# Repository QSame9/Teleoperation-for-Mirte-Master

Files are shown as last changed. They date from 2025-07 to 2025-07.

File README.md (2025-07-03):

# Teleoperation-for-Mirte-Master

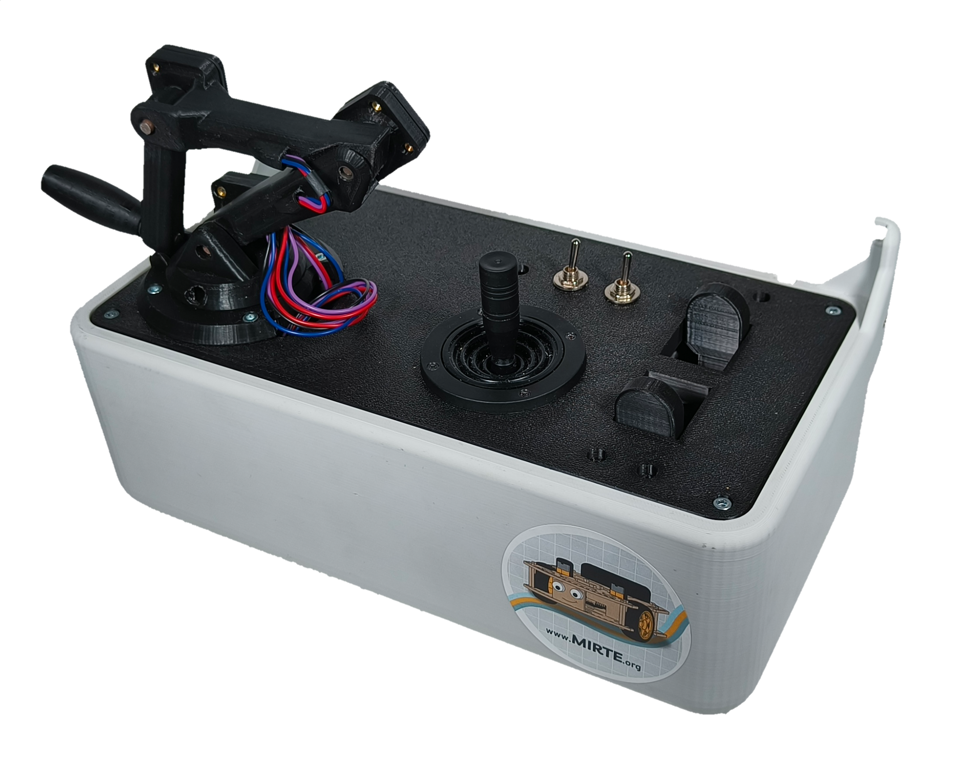
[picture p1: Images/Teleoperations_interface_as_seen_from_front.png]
<figure class="image"><figcaption>Teleoperation interface as seen from front, image by Duncan Bijkerk and Quita Carriere</figcaption></figure>

Authors: Ynze Visser, Quita Carriere, Aditya Swami, Duncan Bijkerk  
Repository: [GitHub page](https://github.com/QSame9/Teleoperation-for-Mirte-Master)  

A physical remote controller interface for the Mirte Master. This project is part of the Bachelor End Project for Mechanical Engineering students at the TU Delft. It was commissioned by the Cognitive Robotics department of the TU Delft.  

# Use of the Teleoperation interface
The Teleoperation interface, here on out also called remote controller, is made for the Mirte Master,  
 often called Mirte, for more info see the [Mirte site](https://mirte.org/) and the [Mirte GitHub](https://github.com/mirte-robot).

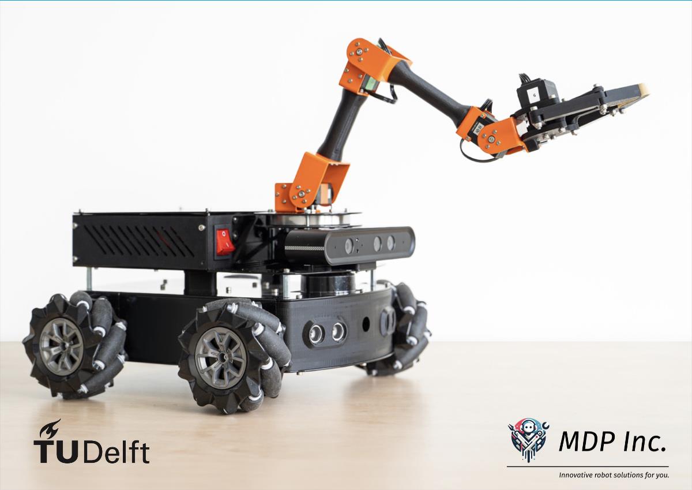
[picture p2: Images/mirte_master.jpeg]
<figure class="image"><figcaption>Mirte Master, image by Chris Pek</figcaption></figure>

The arm movement of the Mirte is controlled by the arm of the controller, mimicking the angular position of each joint. All joints can therefor be controlled in 0th order. To reach the full workspace of the Mirte, a 1st order movement is coded into the periferal working space of the yaw joint of the controller. The Mirte yaw joint can only move 180&deg;, so to reach the back side of the Mirte one of the swithes is made to mirror the movement of all of the arm joints except for the yaw.

The gripper of the Mirte is controlled by the pincher mechanism of the controller, see image below.

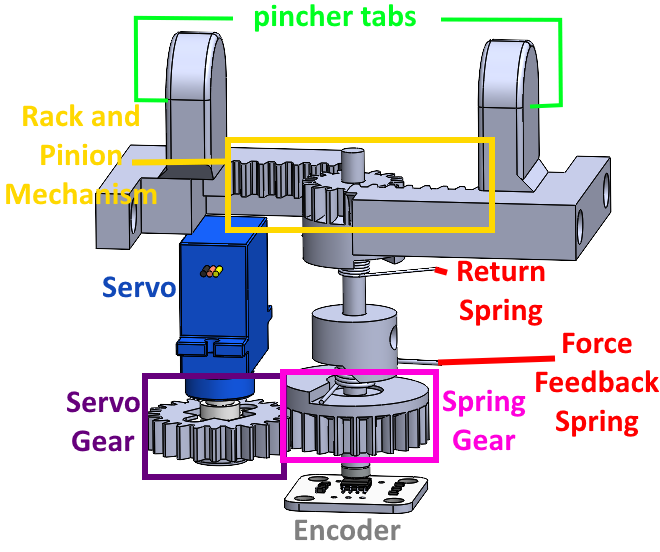
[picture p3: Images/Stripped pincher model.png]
<figure class="image"><figcaption>Pincher CAD close up</figcaption></figure>

Here the linear pinching is transfered via a rack and pinion mechanism to be read out by an angular encoder. This is mapped to the workspace of the gripper. The information is also sent to a force simulator, as to get the force that the force feedback needs to apply. This force feedback is done through Series Elestic Actuation. The servo motor is turned to make the tortion spring compress the correct amount to apply a stiffness to the pincher tabs that the operator holds. The other spring in the mechanism is a return spring, so the tabs open again once the operator lets go.

The driving is done through a simple, off-the-shelf joystick. The Mirte can drive in both holonomic and angular drive methods, and a switch allows for changing the driving style. Due to sensor bias in the joystick, a calibration is done during startup, so the neutral position is determined.

[Here](https://youtube.com/shorts/fPgHeI3LzEk) is a video of the teleoperation interface in action. Some of the delay issues have been resoved since the making of this video.

All the files of the software, CAD models, and electronics can be found in this GitHub repository. The written report for the Bachelor End Project, as well as the presentations given for the course and the files used for analysis can be found in this repository as well.

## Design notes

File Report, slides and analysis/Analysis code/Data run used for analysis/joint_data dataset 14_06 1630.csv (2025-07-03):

t_yaw_enc | data_yaw_enc | t_yaw_mirte | data_yaw_mirte | t_shoulder_enc | data_shoulder_enc | t_shoulder_mirte | data_shoulder_mirte | t_elbow_enc | data_elbow_enc | t_elbow_mirte | data_elbow_mirte | t_wrist_enc | data_wrist_enc | t_wrist_mirte | data_wrist_mirte | t_gripper_enc | data_gripper_enc | t_gripper_mirte | data_gripper_mirte
1.556199312 | -0.03132767 | 2.202921152 | -0.00418879 | 1.589461088 | 1.361505651 | 2.232694387 | 0.963072658 | 1.618501425 | -2.737175102 | 2.273548841 | -1.589994907 | 1.64706707 | -1.562238216 | 2.288056612 | -1.433962464 | 1.676944733 | 0.00644949 | 2.300480366 | 0.446106166
1.570454597 | -0.03132767 | 2.35274744 | 0 | 1.603838921 | 1.361505651 | 3.715931416 | 0.971450269 | 1.639005899 | -2.737175102 | 2.297421455 | -1.594183683 | 1.672877789 | -1.562238216 | 2.353654146 | -1.429773688 | 1.70294404 | 0.00644949 | 2.315000296 | 0.44191736
1.603398561 | -0.03132767 | 2.376379251 | -0.00418879 | 1.640059948 | 1.361505651 | 3.736181498 | 1.000771761 | 1.671754122 | -2.737175102 | 2.315362453 | -1.589994907 | 1.704828024 | -1.562238216 | 2.376704216 | -1.433962464 | 1.735801458 | 0.00644949 | 2.33398509 | 0.433539778
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

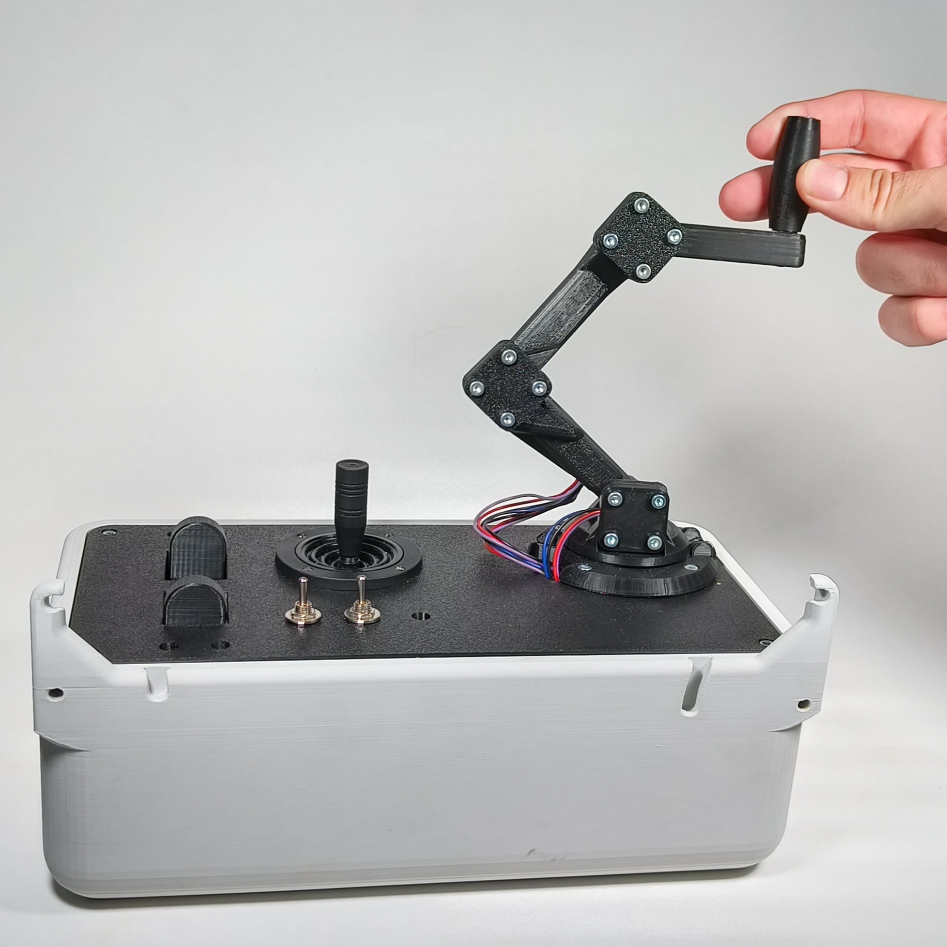
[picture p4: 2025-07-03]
Images/Teleoperations_interface_as_seen_from_operator.jpg

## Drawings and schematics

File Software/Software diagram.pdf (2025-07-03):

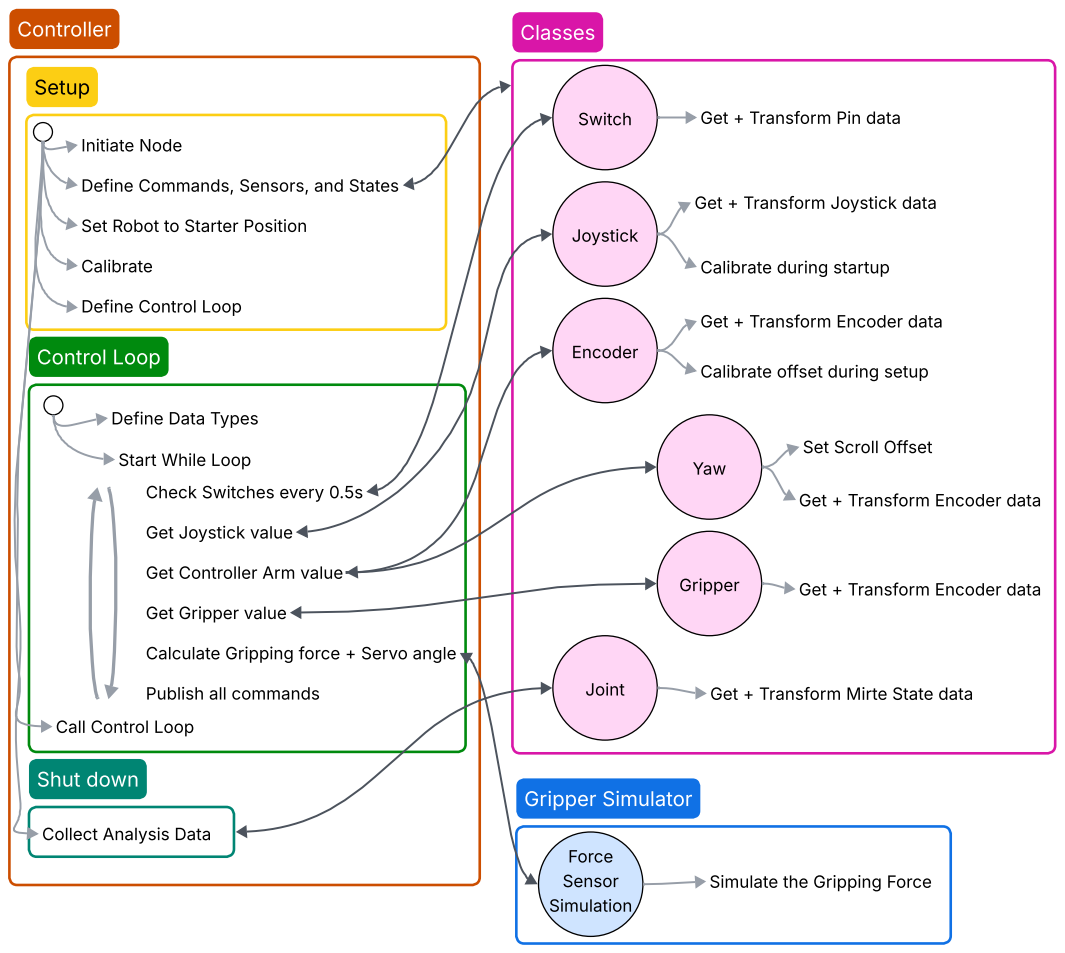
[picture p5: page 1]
Classes; Gripper Simulator; Controller; Setup; Shut down; Encoder; Gripper; Joint; Switch; Joystick; Yaw; Initiate Node; Calibrate; Control Loop; Force Sensor Simulation; Simulate the Gripping; Force

Get + Transform Pin data

Define Commands, Sensors, and States

Get + Transform Joystick data

Set Robot to Starter Position

Calibrate during startup

Define Control Loop

Get + Transform Encoder data

Calibrate offset during setup

Define Data Types

Set Scroll Offset

Start While Loop
Check Switches every 0.5s

Get Joystick value

Get Controller Arm value

Get Gripper value

Calculate Gripping force + Servo angle

Publish all commands

Get + Transform Mirte State data

Call Control Loop

Collect Analysis Data

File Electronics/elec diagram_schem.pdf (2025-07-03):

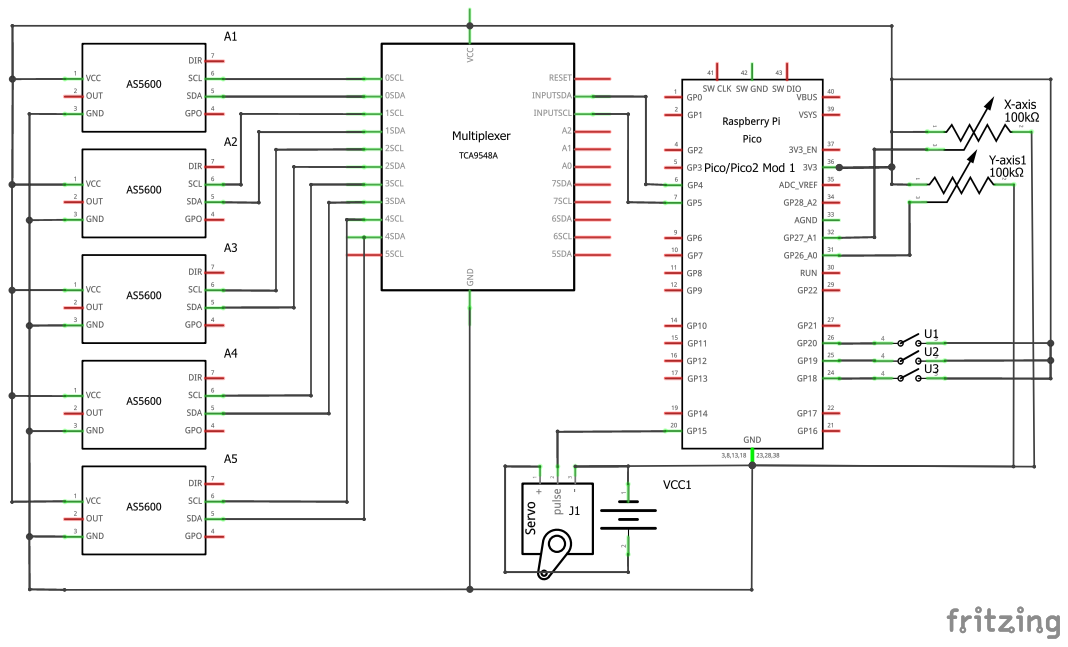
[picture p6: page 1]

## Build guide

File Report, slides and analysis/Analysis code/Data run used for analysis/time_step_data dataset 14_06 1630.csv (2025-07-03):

get switch value | get base input | get arm input | get gripper input | publish base | publish arm | publish gripper | publish servo
0.002441883 | 1.24E-05 | 3.15E-05 | 6.37E-05 | 0.000226259 | 0.000181913 | 0.023518324 | 4.77E-06
2.86E-06 | 1.26E-05 | 2.79E-05 | 5.17E-05 | 0.000206232 | 0.000162125 | 0.010455847 | 5.25E-06
4.05E-06 | 1.67E-05 | 3.39E-05 | 6.32E-05 | 0.000235558 | 0.000165462 | 0.01342535 | 5.25E-06
3.10E-06 | 1.24E-05 | 2.65E-05 | 5.17E-05 | 0.000187397 | 0.000145912 | 0.010587692 | 5.48E-06
3.81E-06 | 1.29E-05 | 3.00E-05 | 4.77E-05 | 0.000200272 | 0.000172138 | 0.015842915 | 4.53E-06
3.10E-06 | 1.19E-05 | 2.62E-05 | 5.05E-05 | 0.000178099 | 0.000131845 | 0.014976025 | 4.29E-06
2.62E-06 | 1.22E-05 | 2.48E-05 | 5.01E-05 | 0.000179291 | 0.000127077 | 0.014565945 | 5.72E-06
3.81E-06 | 1.14E-05 | 2.62E-05 | 5.01E-05 | 0.000178576 | 0.000124454 | 0.011327982 | 5.72E-06
3.81E-06 | 1.05E-05 | 2.53E-05 | 4.60E-05 | 0.000180244 | 0.000198126 | 0.017859936 | 4.77E-06
2.62E-06 | 1.22E-05 | 2.57E-05 | 5.17E-05 | 0.000178099 | 0.000128984 | 0.015555382 | 4.53E-06
3.58E-06 | 1.24E-05 | 2.91E-05 | 4.94E-05 | 0.000240326 | 0.000151873 | 0.013943195 | 3.34E-06
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

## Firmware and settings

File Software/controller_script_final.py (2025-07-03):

"""
Project Name: Teleoperation interface of Mirte Master
File: controller_script_final.py
Description: Does the reading out and the publishing of commands for the Mirte Master

Author: Ynze Visser, Quita Carriere, Aditya Swami, Duncan Bijkerk
License: MIT
Repository: https://github.com/QSame9/Teleoperation-for-Mirte-Master

This file is part of the Bachelor End Project for Mechanical Engineering students at the TU Delft. 
It was commissioned by the Cognitive Robotics department of the TU Delft.


This file is distributed under the terms
of the MIT License. See the LICENSE file in the root of this repository
or visit https://opensource.org/licenses/MIT for more details.
"""
# ---- Import ----
import rospy
import numpy as np
from sensor_classes_final import Encoder, Joystick, Switch, YawEncoder, GripperEncoder, Joint
from gripper_simulator_file_final import GripperSimulator
import math
import csv
import pandas as pd
import time
# import data_collection_script

# load the specific message format required for joint commands
from std_msgs.msg import Float64MultiArray, Float32
from geometry_msgs.msg import Twist
from mirte_msgs.srv import SetServoAngle, GetPinValue, SetPinValue
from mirte_msgs.msg import ServoPosition, Intensity
from sensor_msgs.msg import JointState


# ---- Initialize controller node --------

# start a new ROS node
rospy.init_node('simple_controller_publisher')
# provide on-screen information
rospy.loginfo('The base_controller_publisher has started!')



# ---- Set the publishers and services to control the position of the Mirte Master --------

# create the publisher, tell it which topic to publish on
base_command_publisher = rospy.Publisher('/mobile_base_controller/cmd_vel', Twist, queue_size=10) 
# create the publisher, tell it which topic to publish on
arm_command_publisher = rospy.Publisher('/arm/joint_position_controller/command', Float64MultiArray, queue_size=10)
#create the service, serviceproxy is aan de client side, dus voor het verzenden
set_gripper_angle_service = rospy.ServiceProxy('/mirte/set_servoGripper_servo_angle', SetServoAngle, persistent = True)
set_pincher_servo_angle = rospy.ServiceProxy('/mirte_remote/mirte/set_gripper_cntlr_servo_angle', SetServoAngle, persistent = True)

# ---- General values --------

update_speed = 0.1
stiffness_gripper_spring = 2.08
yaw_offset = 0.51 #yaw on magnet
shoulder_offset = 2.1 #straight up
elbow_offset = 3.13 - 0.5 #straight up
wrist_offset = 4.50 #fully bent inwards
gripper_offset = 2.20 #fully open
servo_offset = math.radians(130) #graden
spring_engagement_angle = 0.60

def callback_states(msg):
    global joint_states_data
    joint_states_data = msg.position

# ---- define sensors on controller --------

yaw_encoder = YawEncoder('/mirte_remote/mirte/encoder/encoders/a', spring_engagement_angle, 
                        calibrating_angle = 0, scaling_factor = 1, first_order_control_gain = 2, offset = yaw_offset)
schoulder_encoder = Encoder('/mirte_remote/mirte/encoder/encoders/b', 
                        calibrating_angle = 0, offset = shoulder_offset)
elbow_encoder = Encoder('/mirte_remote/mirte/encoder/encoders/c', scaling_factor = -1,
                        calibrating_angle = 0, offset = elbow_offset)
wrist_encoder = Encoder('/mirte_remote/mirte/encoder/encoders/d', scaling_factor = -1,
                        calibrating_angle = 1.28, offset = wrist_offset) 
gripper_encoder = GripperEncoder('/mirte_remote/mirte/encoder/encoders/e', 
                        calibrating_angle = 0, offset = gripper_offset, scaling_factor = 1) #checken
joystick = Joystick('/mirte_remote/mirte/intensity/x_axis', 
                        '/mirte_remote/mirte/intensity/y_axis', 0.5 * 1/2040)
gripper_simulator = GripperSimulator()
#joint_states = rospy.Subscriber('/arm/joint_states', JointState, callback_states)

mirte_yaw_joint_state = Joint('/mirte/servos/servoRot/position')
mirte_schoulder_joint_state = Joint('/mirte/servos/servoShoulder/position')
mirte_elbow_joint_state = Joint('/mirte/servos/servoElbow/position')
mirte_wrist_joint_state = Joint('/mirte/servos/servoWrist/position')
mirte_gripper_joint_state = Joint('/mirte/servos/servoGripper/position')

switch_1 = Switch("20")
switch_2 = Switch("19")
switch_3 = Switch("18")


# ---- define robot zero states --------
base_zero = Twist()
base_zero.linear.x = 0.0
base_zero.linear.y = 0.0
base_zero.angular.z = 0.0

arm_up = Float64MultiArray()
arm_up.data = [0,  0.9547413253784178, -2.0481974124908446, -1.418008804321289]

gripper_open = 0.5
pincher_free = 0
# set_pincher_servo_angle(pincher_free)

# ---- Set everything to start position --------
set_gripper_angle_service(gripper_open) #-0.3 is een vinger ertussen 
arm_command_publisher.publish(arm_up)
rospy.sleep(1)
rospy.loginfo('Robot is ready to go!')

print(f"switch_1.value {switch_1.value.data}, switch_2.value {switch_2.value.data}, switch_3.value {switch_3.value.data},")
rospy.sleep(0.1)

# ---- Calibrate joystick
# print("press enter to calibrate yaw on magnet:")
# ready = input()
# yaw_encoder.calibrate()

# print("press enter to calibrate shoulder straight up:")
# ready = input()
# schoulder_encoder.calibrate()

# print("press enter to calibrate elbow straigt up:")
# ready = input()
# elbow_encoder.calibrate()

# print("press enter to calibrate wrist fully bent inwards:")
# ready = input()
# wrist_encoder.calibrate()

# print("press enter to calibrate gripper fully open:")
# ready = input()
# gripper_encoder.calibrate()

# rospy.sleep(0.2)
print('Controller is calibrated! Wil start controlling now!')

def get_switch_values():
    return switch_1.value.data, switch_2.value.data, switch_3.value.data

rospy.sleep(0.1)
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

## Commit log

2025-07-03 Added most BEP files
    The used code, both for controlling and analysis. The electrical diagram from the Pico. The report and analysis csv files that were used for the analysis. CAD models should still be uploaded.
    [elec diagram.fzz, joint_data dataset 14_06 1630.csv, time_step_data dataset 14_06 1630.csv]
2025-07-03 Changed the readme and added slides
    The README now has useful info, some of the files are re-arranged into different folders, and some images and slides were added.
    [joint_data dataset 14_06 1630.csv, time_step_data dataset 14_06 1630.csv]
